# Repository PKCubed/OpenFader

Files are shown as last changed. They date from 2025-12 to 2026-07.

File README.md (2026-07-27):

# OpenFader
### A project to modularize motorized faders with serial daisy chaining.

This board gets soldered onto the back of a motorized fader, and handles the control system aspect of the motorized faders. This board will handle PID control, with different modes and configuration options.
Each board has two UART connections (TX and RX). One UART connection is the upstream connection and connects to the previous fader or to the controller. The other UART connection is the downstream connection and connects to the following fader. When data flows from the controller to the first fader, the controller sends an integer fader address followed by data for that specific fader address. If this integer is not zero, the current fader modifies this address by subtracting 1, then sends the data on to the next fader. This process continuous until the address is zero. At this point, the receiving fader knows that the data is for itself, and it processes the data. Returning data from faders follows the same process but is reversed. Data requested from the fader comes after an address of zero. Each following fader in the path of the data increments this address on its way to the cotnroller. When this address and data gets to the controller, the address will have been incremented such that the controller knows exactly which fader sent this data.

For more protocol details, see the [PROTOCOL.md](PROTOCOL.md) file.

https://github.com/user-attachments/assets/ef170d1e-9a4b-43a3-9d26-493bcd82ac08

PXL_20251116_050939562 RAW-01 MP COVER

I've currently only designed a version for the Behringer MF60T and MF100T, which are some of the most economical motorized faders on the market. For other faders with different pin locations, the circuit is identical, but the locations of the pads will have to be redesigned. For testing, you can always use wires to attach the appropriate PCB pads to the fader.

---

This project is supported by [PCBWay](https://www.pcbway.com/)! I'd like to thank them for sponsoring this project and providing me free prototyping boards. The quality of my initial order is fantastic! They are a great option for PCB manufacturing and component assembly.

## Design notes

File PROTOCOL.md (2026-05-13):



## Hardware
Each fader has two UART connections. One UART connection is upstream, and the other is downstream. This allows an OpenFader board to modify incomming UART data before its sent to the next fader.

## UART Overview
According to the UART protocol defined [here](https://www.analog.com/en/resources/analog-dialogue/articles/uart-a-hardware-communication-protocol.html), a data packet transmission starts with a start bit. During idle state, the data transmission line is held at a high voltage level. This start bit pulls the line low for one clock cycle. Following this start bit are databits. This project uses 8 data bits. Following the data bits is the parity bit which is calculated from the data bits describing the even/oddness of the data, allowing the receiver to detect data validity or corruption. After the parity bit there are 1 to 2 stop bits. These stop bits are high voltage levels.

## UART Daisy-chained Structure
The OpenFader protocol uses two start bytes. These two bytes make up a 16 bit address. Following the start bytes are the payload data. This can be any number of bytes, but these bytes must not match the end byte. After these data bytes is the end byte `0xFF`.

As for the two start bytes, the controller sends out an address as to which OpenFader board in the chain it wants to talk to. This address, anywhere from `0x0000` to `0xFFFE` is sent to the first fader in the chain. When a board receives data, it saves it up until it sees the end byte. At this point, it checks the data it saved. It looks at the address bytes. If the address is `0x0000`, it knows that the data it received was designated for it. It then processes the data, and does not send anything on to the next fader in the chain. If the address is non-zero, it decrements the address by 1, then sends the entire data transmission to the next fader.

When the controller needs data from a fader (position, touch-state, etc.), it will send a request for data using this transmission method. The fader in question will then process the request, and will send its data back. However, instead of sending its actual address in the chain, it sends an address of zero. Then, each following fader on the upstream path back to the controller will increment the address bytes by 1. By the time the controller receives the data, it will see the actual address of the fader that sent the data.

## Data Structure

| Data Byte 0 <br> (Control) | Description |
| --- | --- |
| `0x00` | Read Position |
| `0x01` | Read Error |
| `0x02` | Read Touch |
| `0x10` | Write Position |
| `0x11` | Write LED Color |
| `0x12` | Write Configuration |

## Timing Statistics
Inherent to the method of addressed data transfer used by OpenFader, things are rather inefficient. Each fader in the chain has to buffer the data before it gets to the fader at the end. This causes data transactions to take many uart clock cycles to be completed.

For a 32 fader system assuming a 6 byte transaction <!-- (`Addr0`, `Addr1`, `Control`, `Data1`, `Data2`, `End`) -->running at 115200 baud, a round-trip data transmission to the last fader in the chain would take ___ clock cycles.

A single byte as a UART transaction takes 12 bits. Projecting to a 6 byte transaction, this would take 72 uart clock cycles.

Allowing for a 12 uart cycle processing period, it would take 84*32=2688 uart clock cycles to get the data to the last fader and let the fader process the data. 2688 clock cycles at 115200 Hz gives a transmit time of ~23ms.

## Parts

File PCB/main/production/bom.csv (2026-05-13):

Designator | Footprint | Quantity | Value | LCSC Part #
C2, C5, C7, C8 | C_0402 | 4 | 100nF | C1525
C3, C4 | C_0805 | 2 | 10uF | C15850
R1 | R_0402 | 1 | 10kΩ | C25744
R2 | R_0402 | 1 | 470Ω | C25117
S1, S2 | SW_TS-1088-AR02016 | 2 | Tactile Button, 160gf | C720477
U1 | TSSOP-20_L6.5-W4.4-P0.65-LS6.4-BL | 1 | ~
U5 | so-8 | 1 | L9110 | C513306
U7 | SOT-23-6_L2.9-W1.6-P0.95-LS2.9-BL | 1 | ~

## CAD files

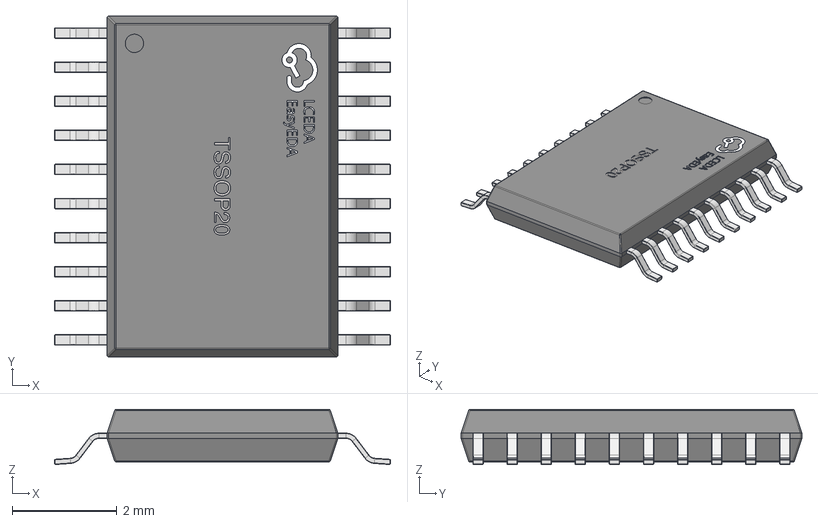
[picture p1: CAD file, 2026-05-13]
PCB/main/EASYEDA_MODELS/TSSOP-20_L6.5-W4.4-H1.0-LS6.4-P0.65.step
6.41 x 6.50 x 1.05 mm

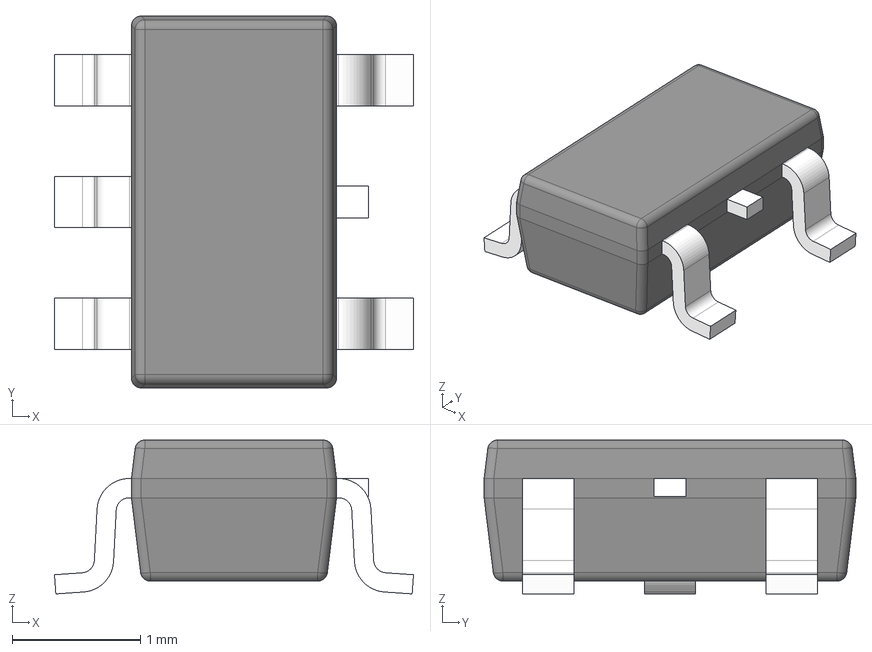
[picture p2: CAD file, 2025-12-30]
PCB/main/Imported Symbols/TLV74033PDBVR/DBV0005A.stp
2.80 x 2.90 x 1.20 mm
BODY-SOT
LEAD-SOT x 5
LEAD-DUMMY

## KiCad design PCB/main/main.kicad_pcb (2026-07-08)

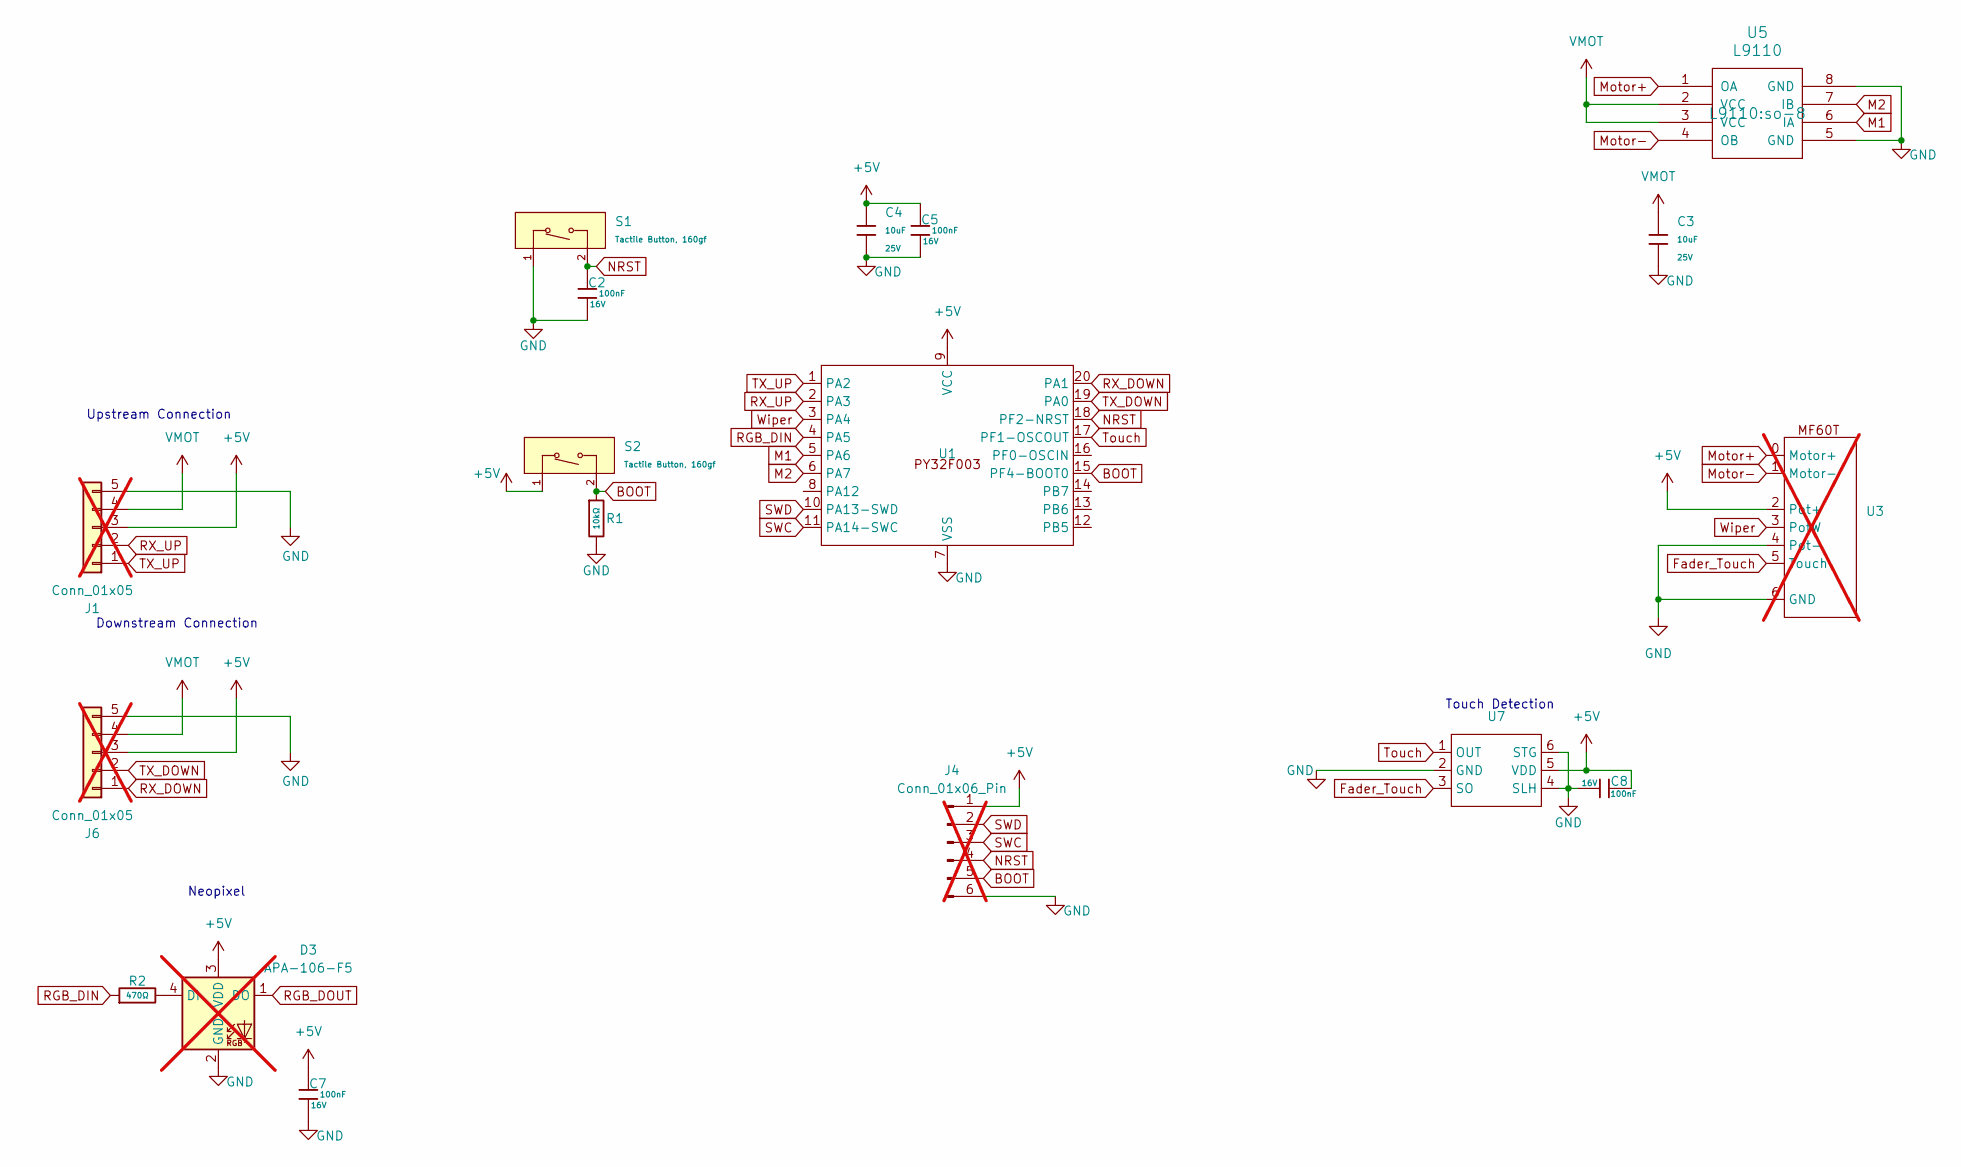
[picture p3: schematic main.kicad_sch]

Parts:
C2, C5, C7, C8: 100nF; C_0402; Voltage Rated 16V; Tolerance ±10%; Part CL05B104KO5NNNC; LCSC C1525
C3, C4: 10uF; C_0805; Voltage Rated 25V; Tolerance ±10%; Part CL21A106KAYNNNE; LCSC C15850
D3: APA-106-F5; LED_D5.0mm-4_RGB; not fitted
J1, J6: Conn_01x05; JST_XH_B5B-XH-AM_1x05_P2.50mm_Vertical; not fitted
J4: Conn_01x06_Pin; PinHeader_1x06_P2.54mm_Vertical; not fitted
R1: 10kΩ; R_0402; Overload Voltage (Max) 50V; Tolerance ±1%; Part 0402WGF1002TCE; LCSC C25744
R2: 470Ω; R_0402; Overload Voltage (Max) 50V; Tolerance ±1%; Part 0402WGF4700TCE; LCSC C25117
S1, S2: Tactile Button, 160gf; SW_TS-1088-AR02016; Voltage Rating (Dc) 12V; Part TS-1088-AR02016; LCSC C720477
U1: TSSOP-20_L6.5-W4.4-P0.65-LS6.4-BL; Part PY32F003F18P6TU; LCSC C5379864
U3: MF60T-MF100T; not fitted
U5: L9110; so-8; LCSC C513306
U7: SOT-23-6_L2.9-W1.6-P0.95-LS2.9-BL; Manufacturer Part TTP223-BA6-TD; LCSC Part Name 单键电容式触摸按键IC

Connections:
+5V: C4.1, C5.1, C7.1, C8.1, D3.3 (VDD), J1.3, J4.1, J6.3, S2.1 (A), U1.9 (VCC), U3.2 (Pot+), U7.5 (VDD)
BOOT: J4.5, R1.1, S2.2 (B), U1.15 (PF4-BOOT0)
Fader_Touch: U3.5 (Touch), U7.3 (SO)
GND: C2.2, C3.2, C4.2, C5.2, C7.2, C8.2, D3.2 (GND), J1.5, J4.6, J6.5, R1.2, S1.1 (A), U1.7 (VSS), U3.4 (Pot-), U3.6 (GND), U5.5 (GND), U5.8 (GND), U7.2 (GND), U7.4 (SLH), U7.6 (STG)
M1: U1.5 (PA6), U5.6 (IA)
M2: U1.6 (PA7), U5.7 (IB)
Motor+: U3.0 (Motor+), U5.1 (OA)
Motor-: U3.1 (Motor-), U5.4 (OB)
NRST: C2.1, J4.4, S1.2 (B), U1.18 (PF2-NRST)
unnamed: D3.4 (DI), R2.2
RGB_DIN: R2.1, U1.4 (PA5)
RGB_DOUT: D3.1 (DO)
RX_DOWN: J6.1, U1.20 (PA1)
RX_UP: J1.2, U1.2 (PA3)
SWC: J4.3, U1.11 (PA14-SWC)
SWD: J4.2, U1.10 (PA13-SWD)
TX_DOWN: J6.2, U1.19 (PA0)
TX_UP: J1.1, U1.1 (PA2)
Touch: U1.17 (PF1-OSCOUT), U7.1 (OUT)
VMOT: C3.1, J1.4, J6.4, U5.2 (VCC), U5.3 (VCC)
Wiper: U1.3 (PA4), U3.3 (PotW)

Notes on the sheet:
Neopixel
Upstream Connection
Touch Detection
Downstream Connection

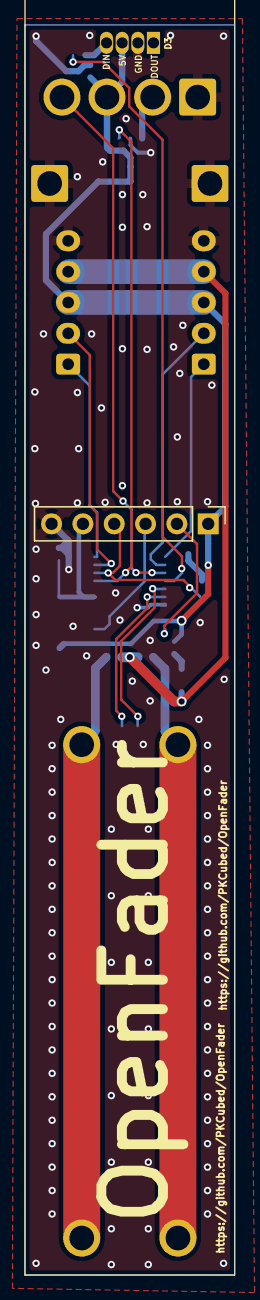
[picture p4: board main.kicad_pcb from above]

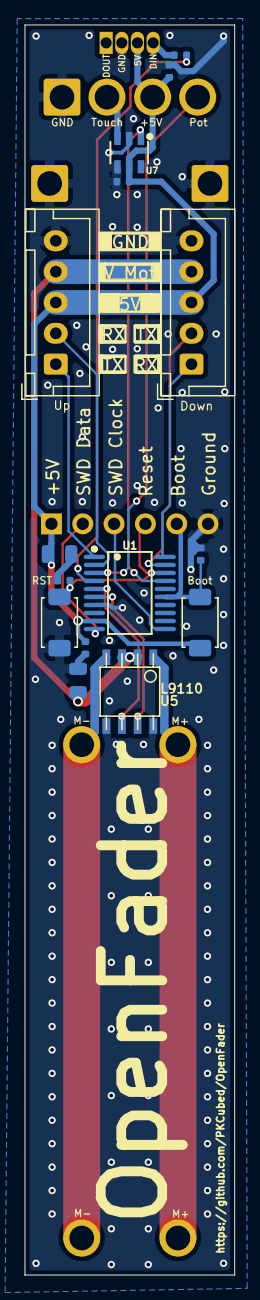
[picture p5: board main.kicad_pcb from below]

Board: 2 copper layers, 17.0 x 101.3 mm, 18 parts (15 on the bottom side), 20 nets.

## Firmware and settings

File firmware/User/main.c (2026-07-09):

#include "py32f0xx_hal.h"
#include "py32f0xx_bsp_printf.h"
#include "ws2812.h"
#include "SEGGER_RTT.h"
#include <math.h>
#include <stdbool.h>

#define VERSION_MAJOR 0
#define VERSION_MINOR 1

void APP_ErrorHandler(void);

ADC_HandleTypeDef AdcHandle;
DMA_HandleTypeDef HdmaCh1;
TIM_HandleTypeDef htim3;

// Global variable where the DMA will automatically drop the latest ADC reading
volatile uint32_t latest_adc_val = 0;

// Basic system clock configuration function
static void APP_SystemClockConfig(void)
{
  RCC_OscInitTypeDef RCC_OscInitStruct = {0};
  RCC_ClkInitTypeDef RCC_ClkInitStruct = {0};

  // HSI Config 24MHz
  RCC_OscInitStruct.OscillatorType = RCC_OSCILLATORTYPE_HSI;
  RCC_OscInitStruct.HSIState = RCC_HSI_ON;
  RCC_OscInitStruct.HSIDiv = RCC_HSI_DIV1;
  RCC_OscInitStruct.HSICalibrationValue = RCC_HSICALIBRATION_24MHz;
  RCC_OscInitStruct.HSEState = RCC_HSE_OFF;
  RCC_OscInitStruct.LSIState = RCC_LSI_OFF;
  if (HAL_RCC_OscConfig(&RCC_OscInitStruct) != HAL_OK)
  {
    APP_ErrorHandler();
  }

  // SysClk Config
  RCC_ClkInitStruct.ClockType = RCC_CLOCKTYPE_HCLK | RCC_CLOCKTYPE_SYSCLK | RCC_CLOCKTYPE_PCLK1;
  RCC_ClkInitStruct.SYSCLKSource = RCC_SYSCLKSOURCE_HSI;
  RCC_ClkInitStruct.AHBCLKDivider = RCC_SYSCLK_DIV1;
  RCC_ClkInitStruct.APB1CLKDivider = RCC_HCLK_DIV1;
  if (HAL_RCC_ClockConfig(&RCC_ClkInitStruct, FLASH_LATENCY_0) != HAL_OK)
  {
    APP_ErrorHandler();
  }
}



// Override the weak _write function so printf outputs to SEGGER RTT
int _write(int file, char *ptr, int len) {
  (void)file;
  SEGGER_RTT_Write(0, ptr, len);
  return len;
}

// Initialize ADC to read analog voltage from PA4 (Channel 4) via DMA
static void APP_ADC_Init(void)
{
  // Reset the ADC hardware state before configuration
  __HAL_RCC_ADC_FORCE_RESET();
  __HAL_RCC_ADC_RELEASE_RESET();
  
  // Enable clocks for ADC, GPIOA, SYSCFG (for DMA mapping), and DMA
  __HAL_RCC_ADC_CLK_ENABLE();
  __HAL_RCC_GPIOA_CLK_ENABLE();
  __HAL_RCC_SYSCFG_CLK_ENABLE();
  __HAL_RCC_DMA_CLK_ENABLE();

  // Configure PA4 specifically as an analog input pin
  GPIO_InitTypeDef GPIO_InitStruct = {0};
  GPIO_InitStruct.Pin = GPIO_PIN_4;                   // Select pin PA4
  GPIO_InitStruct.Mode = GPIO_MODE_ANALOG;            // Put it into analog mode
  GPIO_InitStruct.Pull = GPIO_NOPULL;                 // No internal pull-ups or pull-downs
  HAL_GPIO_Init(GPIOA, &GPIO_InitStruct);

  // --- DMA CONFIGURATION ---
  // Map the ADC DMA request to DMA Channel 1
  HAL_SYSCFG_DMA_Req(DMA_CHANNEL_MAP_ADC);

  // Configure DMA Channel 1 to move data from Peripheral to Memory
  HdmaCh1.Instance                 = DMA1_Channel1;
  HdmaCh1.Init.Direction           = DMA_PERIPH_TO_MEMORY;
  HdmaCh1.Init.PeriphInc           = DMA_PINC_DISABLE;         // Always read from the exact same ADC register
  HdmaCh1.Init.MemInc              = DMA_MINC_DISABLE;         // Always write to the exact same variable (latest_adc_val)
  HdmaCh1.Init.PeriphDataAlignment = DMA_PDATAALIGN_HALFWORD;  // ADC data register is 16-bit
  HdmaCh1.Init.MemDataAlignment    = DMA_MDATAALIGN_WORD;      // Our variable is 32-bit
  HdmaCh1.Init.Mode                = DMA_CIRCULAR;             // Keep looping endlessly (Continuous mode)
  HdmaCh1.Init.Priority            = DMA_PRIORITY_HIGH;        // High priority for ADC data

  // Initialize the DMA channel
  HAL_DMA_Init(&HdmaCh1);
  
  // Link this DMA handle to our ADC handle
  __HAL_LINKDMA(&AdcHandle, DMA_Handle, HdmaCh1);

  // --- ADC CONFIGURATION ---
  AdcHandle.Instance = ADC1;
  
  // Run an internal calibration sequence on the ADC for accurate readings
  if (HAL_ADCEx_Calibration_Start(&AdcHandle) != HAL_OK)
  {
    APP_ErrorHandler();
  }
  
  // Configure the general ADC operation
  AdcHandle.Init.ClockPrescaler        = ADC_CLOCK_SYNC_PCLK_DIV1;
  AdcHandle.Init.Resolution            = ADC_RESOLUTION_12B;
  AdcHandle.Init.DataAlign             = ADC_DATAALIGN_RIGHT;
  AdcHandle.Init.ScanConvMode          = ADC_SCAN_DIRECTION_FORWARD;
  AdcHandle.Init.EOCSelection          = ADC_EOC_SINGLE_CONV;
  AdcHandle.Init.LowPowerAutoWait      = ENABLE;                   // Enable auto-wait for stability during continuous conversions
  AdcHandle.Init.ContinuousConvMode    = ENABLE;                   // **NEW**: Automatically start next reading!
  AdcHandle.Init.DiscontinuousConvMode = DISABLE;
  AdcHandle.Init.ExternalTrigConv      = ADC_SOFTWARE_START;
  AdcHandle.Init.ExternalTrigConvEdge  = ADC_EXTERNALTRIGCONVEDGE_NONE;
  AdcHandle.Init.DMAContinuousRequests = ENABLE;                   // **NEW**: Tell ADC to constantly push data to DMA!
  AdcHandle.Init.Overrun               = ADC_OVR_DATA_OVERWRITTEN;
  AdcHandle.Init.SamplingTimeCommon    = ADC_SAMPLETIME_239CYCLES_5;
  
  // Apply the ADC configuration
  if (HAL_ADC_Init(&AdcHandle) != HAL_OK)
  {
    APP_ErrorHandler();
  }

  // Link our configured ADC specifically to Channel 4 (which maps to PA4)
  ADC_ChannelConfTypeDef sConfig = {0};
  sConfig.Rank         = ADC_RANK_CHANNEL_NUMBER;
  sConfig.Channel      = ADC_CHANNEL_4;
  
  // Apply channel configuration
  if (HAL_ADC_ConfigChannel(&AdcHandle, &sConfig) != HAL_OK)
  {
    APP_ErrorHandler();
  }

  // START the ADC and link it to our target variable via DMA (buffer size 1)
  if (HAL_ADC_Start_DMA(&AdcHandle, (uint32_t*)&latest_adc_val, 1) != HAL_OK)
  {
    APP_ErrorHandler();
  }
}

// Initialize TIM3 to generate a PWM signal on PA6 and PA7 for the motor driver
static void APP_TIM3_PWM_Init(void)
{
  // Enable the clock for TIM3 peripheral
  __HAL_RCC_TIM3_CLK_ENABLE();
  
  // Enable the clock for GPIOA port
  __HAL_RCC_GPIOA_CLK_ENABLE();
  
  // Configure PA6 (TIM3_CH1) and PA7 (TIM3_CH2) pins for Alternate Function Push-Pull mode
  GPIO_InitTypeDef GPIO_InitStruct = {0};
  GPIO_InitStruct.Pin = GPIO_PIN_6 | GPIO_PIN_7;
  GPIO_InitStruct.Mode = GPIO_MODE_AF_PP;
  GPIO_InitStruct.Pull = GPIO_NOPULL;
  GPIO_InitStruct.Speed = GPIO_SPEED_FREQ_HIGH;
  GPIO_InitStruct.Alternate = GPIO_AF1_TIM3;
  HAL_GPIO_Init(GPIOA, &GPIO_InitStruct);

  // Configure the TIM3 time base (frequency)
  htim3.Instance = TIM3;
  htim3.Init.Prescaler = 10 - 1;                      // 2.4MHz timer clock (24MHz / 10)
  htim3.Init.CounterMode = TIM_COUNTERMODE_UP;
  htim3.Init.Period = 100 - 1;                        // 24kHz PWM frequency (2.4MHz / 100)
  htim3.Init.ClockDivision = TIM_CLOCKDIVISION_DIV1;
  htim3.Init.AutoReloadPreload = TIM_AUTORELOAD_PRELOAD_ENABLE;
  if (HAL_TIM_PWM_Init(&htim3) != HAL_OK)
  {
    APP_ErrorHandler();
  }

  // Configure the specific PWM channels
  TIM_OC_InitTypeDef sConfigOC = {0};
  sConfigOC.OCMode = TIM_OCMODE_PWM1;
  sConfigOC.Pulse = 0;                                // Initial duty cycle: 0%
  sConfigOC.OCPolarity = TIM_OCPOLARITY_HIGH;
  sConfigOC.OCFastMode = TIM_OCFAST_DISABLE;
  
  if (HAL_TIM_PWM_ConfigChannel(&htim3, &sConfigOC, TIM_CHANNEL_1) != HAL_OK)
  {
    APP_ErrorHandler();
  }
  
  if (HAL_TIM_PWM_ConfigChannel(&htim3, &sConfigOC, TIM_CHANNEL_2) != HAL_OK)
  {
    APP_ErrorHandler();
  }
  
  // Start the PWM generation
  HAL_TIM_PWM_Start(&htim3, TIM_CHANNEL_1);
  HAL_TIM_PWM_Start(&htim3, TIM_CHANNEL_2);
}

// Helper function to easily control the motor speed and direction
// speed ranges from -100 (full speed down) to +100 (full speed up)
void APP_Motor_SetSpeed(int speed)
{
  // Clamp speed to safe limits
  if (speed > 100) speed = 100;
  if (speed < -100) speed = -100;
  
  if (speed > 0)
  {
    // Move UP (Increase ADC): PA7 gets PWM, PA6 is grounded
    __HAL_TIM_SET_COMPARE(&htim3, TIM_CHANNEL_1, 0);
    __HAL_TIM_SET_COMPARE(&htim3, TIM_CHANNEL_2, speed);
  }
  else if (speed < 0)
  {
    // Move DOWN (Decrease ADC): PA6 gets PWM, PA7 is grounded (use absolute value of speed)
    __HAL_TIM_SET_COMPARE(&htim3, TIM_CHANNEL_1, -speed);
    __HAL_TIM_SET_COMPARE(&htim3, TIM_CHANNEL_2, 0);
  }
  else
  {
    // Stop: Both grounded
    __HAL_TIM_SET_COMPARE(&htim3, TIM_CHANNEL_1, 0);
    __HAL_TIM_SET_COMPARE(&htim3, TIM_CHANNEL_2, 0);
  }
}


int main(void)
{
  // Initialize the Hardware Abstraction Layer (HAL)
  HAL_Init();
  
  // Configure the system clocks (running at 24MHz HSI)
  APP_SystemClockConfig();
  
  // Initialize SEGGER RTT for seamless console output over SWD
  SEGGER_RTT_Init();
  
  // Print a startup message to the RTT terminal
  printf("OpenFader v%i.%i\r\nSystem Clock: %ld\r\n", VERSION_MAJOR, VERSION_MINOR, SystemCoreClock);

  // Initialize the custom ADC configuration on PA4
  APP_ADC_Init();
  
  // Initialize the motor PWM on PA6 and PA7
  APP_TIM3_PWM_Init();
  
  /*
  // Good PID Controller Settings
  float kp = 0.015f;
  float ki = 0.005f;
  float kd = 2.5f;
  */

  float kp = 0.06f;
  float ki = 0.005f;
  float kd = 0.5f;
  
  bool enable_deadzones = false; // Set to false to completely disable all deadzones for testing
  int deadzone = 10;       // Stop motor when error falls below this
  int deadzone_exit = 25;  // Don't wake up until error exceeds this (Hysteresis)
  int d_deadzone = 25;     // Ignore D-term changes smaller than this to stop jitter
  
  int min_pwm = 55;        // Minimum PWM required to overcome physical friction
  float max_i_term = 30.0f; // Maximum PWM power the I-term is allowed to add
  
  // Anti-Windup Settings
  int i_active_zone = 200; // Only integrate when error is smaller than this (prevents windup on long travels)
  
  float previous_error = 0.0f;
  float integral = 0.0f;
  bool motor_enabled = true;
  bool is_resting = false; // Hysteresis state tracker
  
  uint32_t last_pid_time = HAL_GetTick();
  uint32_t last_print_time = HAL_GetTick();
  
  // Variables to hold state for printing
  int current_setpoint = 2048;
  float current_error = 0.0f;
  int current_motor_speed = 0;

  // ADC Filtering settings
  float filtered_adc = 0.0f;
  float alpha = 0.2f; // Smoothing factor: lower = smoother but more lag, 1.0 = no smoothing

  while (1)
  {
    uint32_t current_time = HAL_GetTick();

    // --- 1. Fast PID Loop (Runs every 1ms = 1000Hz) ---
    if (current_time - last_pid_time >= 1)
    {
      last_pid_time = current_time;

      // Generate a sine wave setpoint based on system time
      float time_sec = current_time / 1000.0f;
      
      // Uncomment to test sine wave: 
      current_setpoint = 2048 + (int)(1900.0f * sin(time_sec));


      // Apply Exponential Moving Average (EMA) Filter to ADC readings
      if (filtered_adc == 0.0f) filtered_adc = (float)latest_adc_val; // Initialize on first run
      filtered_adc = (alpha * (float)latest_adc_val) + ((1.0f - alpha) * filtered_adc);

      if (motor_enabled)
      {
        // 1. Calculate Error (Target - Current Position)
        current_error = (float)current_setpoint - filtered_adc;
        
        // Hysteresis check to prevent chattering on the boundary
        if (enable_deadzones)
        {
          if (!is_resting && current_error >= -deadzone && current_error <= deadzone)
          {
            is_resting = true; // Enter resting state
          }
          else if (is_resting && (current_error > deadzone_exit || current_error < -deadzone_exit))
          {
            is_resting = false; // Wake up from resting state
          }
        }
        else
        {
          is_resting = false; // Never rest if deadzones are disabled
        }
        
        if (is_resting)
        {
          // We are close enough to the target! Stop the motor and clear integral buildup
          current_error = 0.0f;
          integral = 0.0f; 
          current_motor_speed = 0;
          previous_error = 0.0f;
          
          APP_Motor_SetSpeed(0);
        }
        else
        {
          // 2. Calculate PID terms
          
          // Integration Window: Only integrate when we are relatively close to the target.
          // If we are far away, the P-term has plenty of power, and integrating would just 
          // build up a massive windup debt while traveling or if physically held.
          if (current_error > -i_active_zone && current_error < i_active_zone)
          {
            integral += current_error;
          }
          else
          {
            integral = 0.0f; 
          }
          
          // Anti-windup for the integral term
          // Dynamically clamp the integral so it can't contribute more than max_i_term
          float max_integral = ki > 0.0f ? (max_i_term / ki) : 0.0f;
          if (integral > max_integral) integral = max_integral;
          if (integral < -max_integral) integral = -max_integral;
          
          float derivative = current_error - previous_error;
          
          // Disable D term when we are within N counts from the setpoint
          // to prevent the D-term from reacting to high-frequency noise near the target
          if (enable_deadzones && current_error > -d_deadzone && current_error < d_deadzone)
          {
            derivative = 0.0f;
          }
          
          // Calculate P, I, D components separately
          float p_term = kp * current_error;
          float i_term = ki * integral;
          float d_term = kd * derivative;
        
          // Apply stiction compensation (min_pwm) exclusively to the P-term.
          // This gives the D-term and I-term full linear authority to smoothly brake
          // the motor all the way down to 0 (and even into negative for active braking)
          // without triggering a violent +/- 60% jump in PWM.
          if (p_term > 0)
          {
            p_term += min_pwm;
          }
          else if (p_term < 0)
          {
            p_term -= min_pwm;
          }
        
          // 3. Compute the final motor speed (-100 to 100)
          float output = p_term + i_term + d_term;
          current_motor_speed = (int)output;
        
          // 4. Drive the Motor
          APP_Motor_SetSpeed(current_motor_speed);
          
          previous_error = current_error;
        }
      }
      else
      {
        // Motor is disabled - Let the user control it manually
        APP_Motor_SetSpeed(0);
      }
    }

    // --- 2. Slow Print Loop (Runs every 100ms = 10Hz) ---
    if (current_time - last_print_time >= 100)
    {
      last_print_time = current_time;
      
      if (motor_enabled)
      {
        printf("SP: %d | ADC: %d | ERR: %d | OUT: %d\r\n", current_setpoint, (int)filtered_adc, (int)current_error, current_motor_speed);
      }
      else
      {
        printf("Motor Disabled | ADC: %d\r\n", (int)filtered_adc);
      }
    }
  }
}

void APP_ErrorHandler(void) {
  while (1);
}

#ifdef  USE_FULL_ASSERT
void assert_failed(uint8_t *file, uint32_t line) {
  while (1);
}
#endif /* USE_FULL_ASSERT */

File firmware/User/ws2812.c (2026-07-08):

#include "ws2812.h"
#include "py32f0xx_hal.h"
#include <string.h>

TIM_HandleTypeDef htim1;
DMA_HandleTypeDef hdma_tim1_up;

#define WS2812_HIGH WS2812_PIN
#define WS2812_LOW (WS2812_PIN << 16)

uint32_t ws2812_dma_buffer[72];
volatile uint8_t ws2812_dma_ready = 1;

void WS2812_DmaCplt(DMA_HandleTypeDef *hdma) {
    // Stop timer and DMA
    HAL_TIM_Base_Stop(&htim1);
    __HAL_TIM_DISABLE_DMA(&htim1, TIM_DMA_UPDATE);
    
    // Ensure pin is low after transfer
    WS2812_PORT->BRR = WS2812_PIN;
    
    ws2812_dma_ready = 1;
}

void DMA1_Channel1_IRQHandler(void) {
    HAL_DMA_IRQHandler(&hdma_tim1_up);
}

void WS2812_Init(void) {
    // 1. Enable Clocks
    __HAL_RCC_GPIOA_CLK_ENABLE();
    __HAL_RCC_TIM1_CLK_ENABLE();
    __HAL_RCC_DMA_CLK_ENABLE();
    __HAL_RCC_SYSCFG_CLK_ENABLE();

    // 2. GPIO Init (PA5 as Output)
    GPIO_InitTypeDef GPIO_InitStruct = {0};
    GPIO_InitStruct.Pin = WS2812_PIN;
    GPIO_InitStruct.Mode = GPIO_MODE_OUTPUT_PP;
    GPIO_InitStruct.Pull = GPIO_NOPULL;
    GPIO_InitStruct.Speed = GPIO_SPEED_FREQ_VERY_HIGH;
    HAL_GPIO_Init(WS2812_PORT, &GPIO_InitStruct);
    HAL_GPIO_WritePin(WS2812_PORT, WS2812_PIN, GPIO_PIN_RESET);

    // 3. DMA Channel Init
    hdma_tim1_up.Instance = DMA1_Channel1;
    hdma_tim1_up.Init.Direction = DMA_MEMORY_TO_PERIPH;
    hdma_tim1_up.Init.PeriphInc = DMA_PINC_DISABLE;
    hdma_tim1_up.Init.MemInc = DMA_MINC_ENABLE;
    hdma_tim1_up.Init.PeriphDataAlignment = DMA_PDATAALIGN_WORD;
    hdma_tim1_up.Init.MemDataAlignment = DMA_MDATAALIGN_WORD;
    hdma_tim1_up.Init.Mode = DMA_NORMAL;
    hdma_tim1_up.Init.Priority = DMA_PRIORITY_VERY_HIGH;
    HAL_DMA_Init(&hdma_tim1_up);

    // Register callback manually
    hdma_tim1_up.XferCpltCallback = WS2812_DmaCplt;

    // 4. Map TIM1_UP to DMA1 Channel 1 via SYSCFG
    // LL_SYSCFG_DMA_MAP_TIM1_UP is 0x10 for DMA1_CH1 (bits 4:0 in CFGR3)
    SYSCFG->CFGR3 = (SYSCFG->CFGR3 & ~0x1FUL) | 0x10UL;

    // 5. Link DMA to TIM1
    __HAL_LINKDMA(&htim1, hdma[TIM_DMA_ID_UPDATE], hdma_tim1_up);

    // 6. DMA Interrupt
    HAL_NVIC_SetPriority(DMA1_Channel1_IRQn, 0, 0);
    HAL_NVIC_EnableIRQ(DMA1_Channel1_IRQn);

    // 7. TIM1 Init
    htim1.Instance = TIM1;
    htim1.Init.Prescaler = 0;
    htim1.Init.CounterMode = TIM_COUNTERMODE_UP;
    htim1.Init.Period = 9; // 24MHz / 10 = 2.4MHz (416.6ns per DMA transfer)
    htim1.Init.ClockDivision = TIM_CLOCKDIVISION_DIV1;
    htim1.Init.AutoReloadPreload = TIM_AUTORELOAD_PRELOAD_DISABLE;
    HAL_TIM_Base_Init(&htim1);
}

void WS2812_SendPixel(uint8_t r, uint8_t g, uint8_t b) {
    // Wait until previous transfer finishes
    while(!ws2812_dma_ready);
    ws2812_dma_ready = 0;

    // WS2812 expects GRB order
    uint32_t grb = (g << 16) | (r << 8) | b;
    uint32_t idx = 0;
    
    // Each bit is represented by 3 DMA transfers to BSRR
    for (int i = 23; i >= 0; i--) {
        if (grb & (1 << i)) {
            // Logic 1: High, High, Low
            ws2812_dma_buffer[idx++] = WS2812_HIGH;
            ws2812_dma_buffer[idx++] = WS2812_HIGH;
            ws2812_dma_buffer[idx++] = WS2812_LOW;
        } else {
            // Logic 0: High, Low, Low
            ws2812_dma_buffer[idx++] = WS2812_HIGH;
            ws2812_dma_buffer[idx++] = WS2812_LOW;
            ws2812_dma_buffer[idx++] = WS2812_LOW;
        }
    }

    // Start DMA transfer
    HAL_DMA_Start_IT(&hdma_tim1_up, (uint32_t)ws2812_dma_buffer, (uint32_t)&WS2812_PORT->BSRR, 72);
    
    // Enable TIM Update DMA Request
    __HAL_TIM_ENABLE_DMA(&htim1, TIM_DMA_UPDATE);
    
    // Start TIM1
    HAL_TIM_Base_Start(&htim1);
}

void WS2812_Show(void) {
    // A delay of >50us causes the WS2812 to latch the data.
    // HAL_Delay(1) is 1ms, which is plenty.
    HAL_Delay(1);
}

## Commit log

2025-11-02 Expand README with I2C Registers section
    Added detailed I2C register information for the OpenFader project.
2025-12-30 Added PCB Rev 1 Files
    [DBV0005A.stp, bom.csv, designators.csv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]
2026-04-11 Initial commit on rp2040 version
    Switching to the cheaper, more capable RP2040 with an additional change from the I2C protocol to a daisy-chained serial protocol.
    [main.kicad_sch]
2026-04-12 Progress on new PCB schematic
    [main.kicad_sch]
2026-04-12 Progress on schematic
    [main.kicad_sch]
2026-05-08 Schematic Updates
    [SOT-23-6_L2.9-W1.6-P0.95-LS2.9-BL.step, main.kicad_sch]
2026-05-09 Started new branch
    [TSSOP-20_L6.5-W4.4-H1.0-LS6.4-P0.65.step, main.kicad_sch]
2026-05-09 PCB Nearly Complete
    [main.kicad_pcb, main.kicad_sch]
2026-05-09 PCB Updates
    [SOP-8_L4.9-W3.9-P1.27-LS6.0-BL-1.step, main.kicad_pcb, main.kicad_sch]
2026-05-11 Set components to DNP
    [main.kicad_sch]
2026-05-12 Progress on PCB
    Flipped side of board for components
    [main.kicad_pcb, main.kicad_sch]
2026-05-13 PCB Progress
    [SOP-8_L4.9-W3.9-P1.27-LS6.0-BL-1.step, SOT-23-6_L2.9-W1.6-P0.95-LS2.9-BL.step, TSSOP-20_L6.5-W4.4-H1.0-LS6.4-P0.65.step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]
2026-05-13 PCB Final Draft
    [TSSOP-20_L6.5-W4.4-H1.0-LS6.4-P0.65.step, main.kicad_pcb]
2026-05-13 Generated Fab Files
    [bom.csv, designators.csv, positions.csv]
2026-05-13 Revise README with project details and updates
    Updated project description and added details about UART connections and supported faders. Removed I2C register section and mentioned upcoming PCB development.
2026-05-13 Update PROTOCOL.md with UART connection details
    Added description of UART connections for faders.
2026-05-13 Fix spelling and enhance UART protocol explanation
    Corrected spelling of 'incoming' and improved clarity of UART protocol description.
2026-05-13 Enhance PROTOCOL.md with hardware and UART details
    Added detailed sections on hardware, UART overview, daisy-chained structure, and data structure to PROTOCOL.md.
2026-06-12 Acknowledge PCBWay support in README
    Added acknowledgment for PCBWay's support and sponsorship.
